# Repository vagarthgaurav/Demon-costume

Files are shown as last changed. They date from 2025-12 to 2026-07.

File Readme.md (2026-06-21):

# Demon Costume

This project is the electronics part of a demon costume. The costume is a work in progress. The hardware design is completed. It will be eventually be integrated into the costume which is intended to be worn in festivals. 

It contains three custom PCBs. The wings open and close driven by linear actuators. It can also drive multiple RGB led chains. It is controlled wirelessly with a remote.

---

## demonBoard



The Main controller. ESP32-C3 Wroom drives two linear actuators for the wings and has connectors for the LED boards. It is powered by a 3S Lipo. 

---

## demonSpawn



The remote that controls the main board. Also an ESP32-C3 Wroom, talks to the demonBoard over ESP-now protocol. It is powered by 18650 Li-Ion cell with USB-C charging. Has 5V LED outputs so it can be integrated into something like a sword.

---

## demonLight



Small board with a single WS2813B RGB LED. Boards can be chained together and they are screwed onto 3D printed thorns.



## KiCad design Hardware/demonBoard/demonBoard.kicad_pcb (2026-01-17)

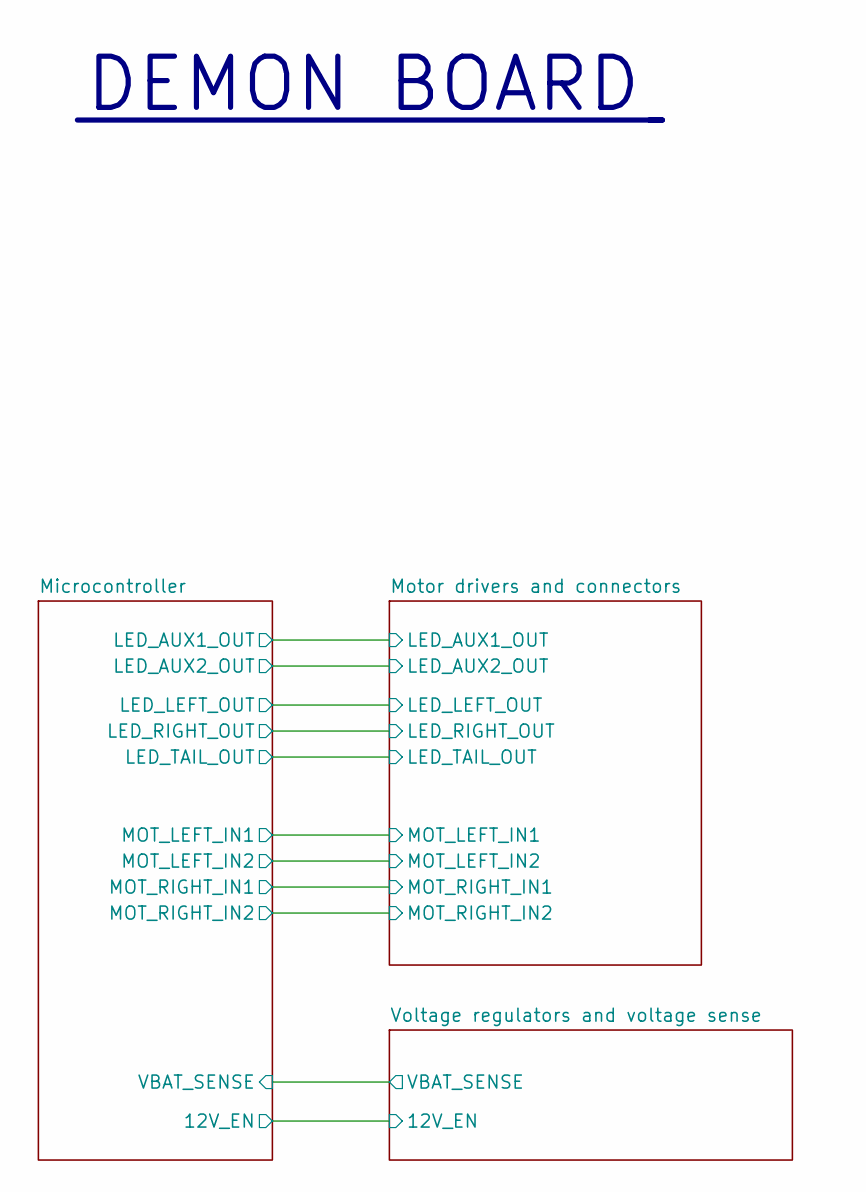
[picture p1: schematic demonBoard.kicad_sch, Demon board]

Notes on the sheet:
DEMON BOARD

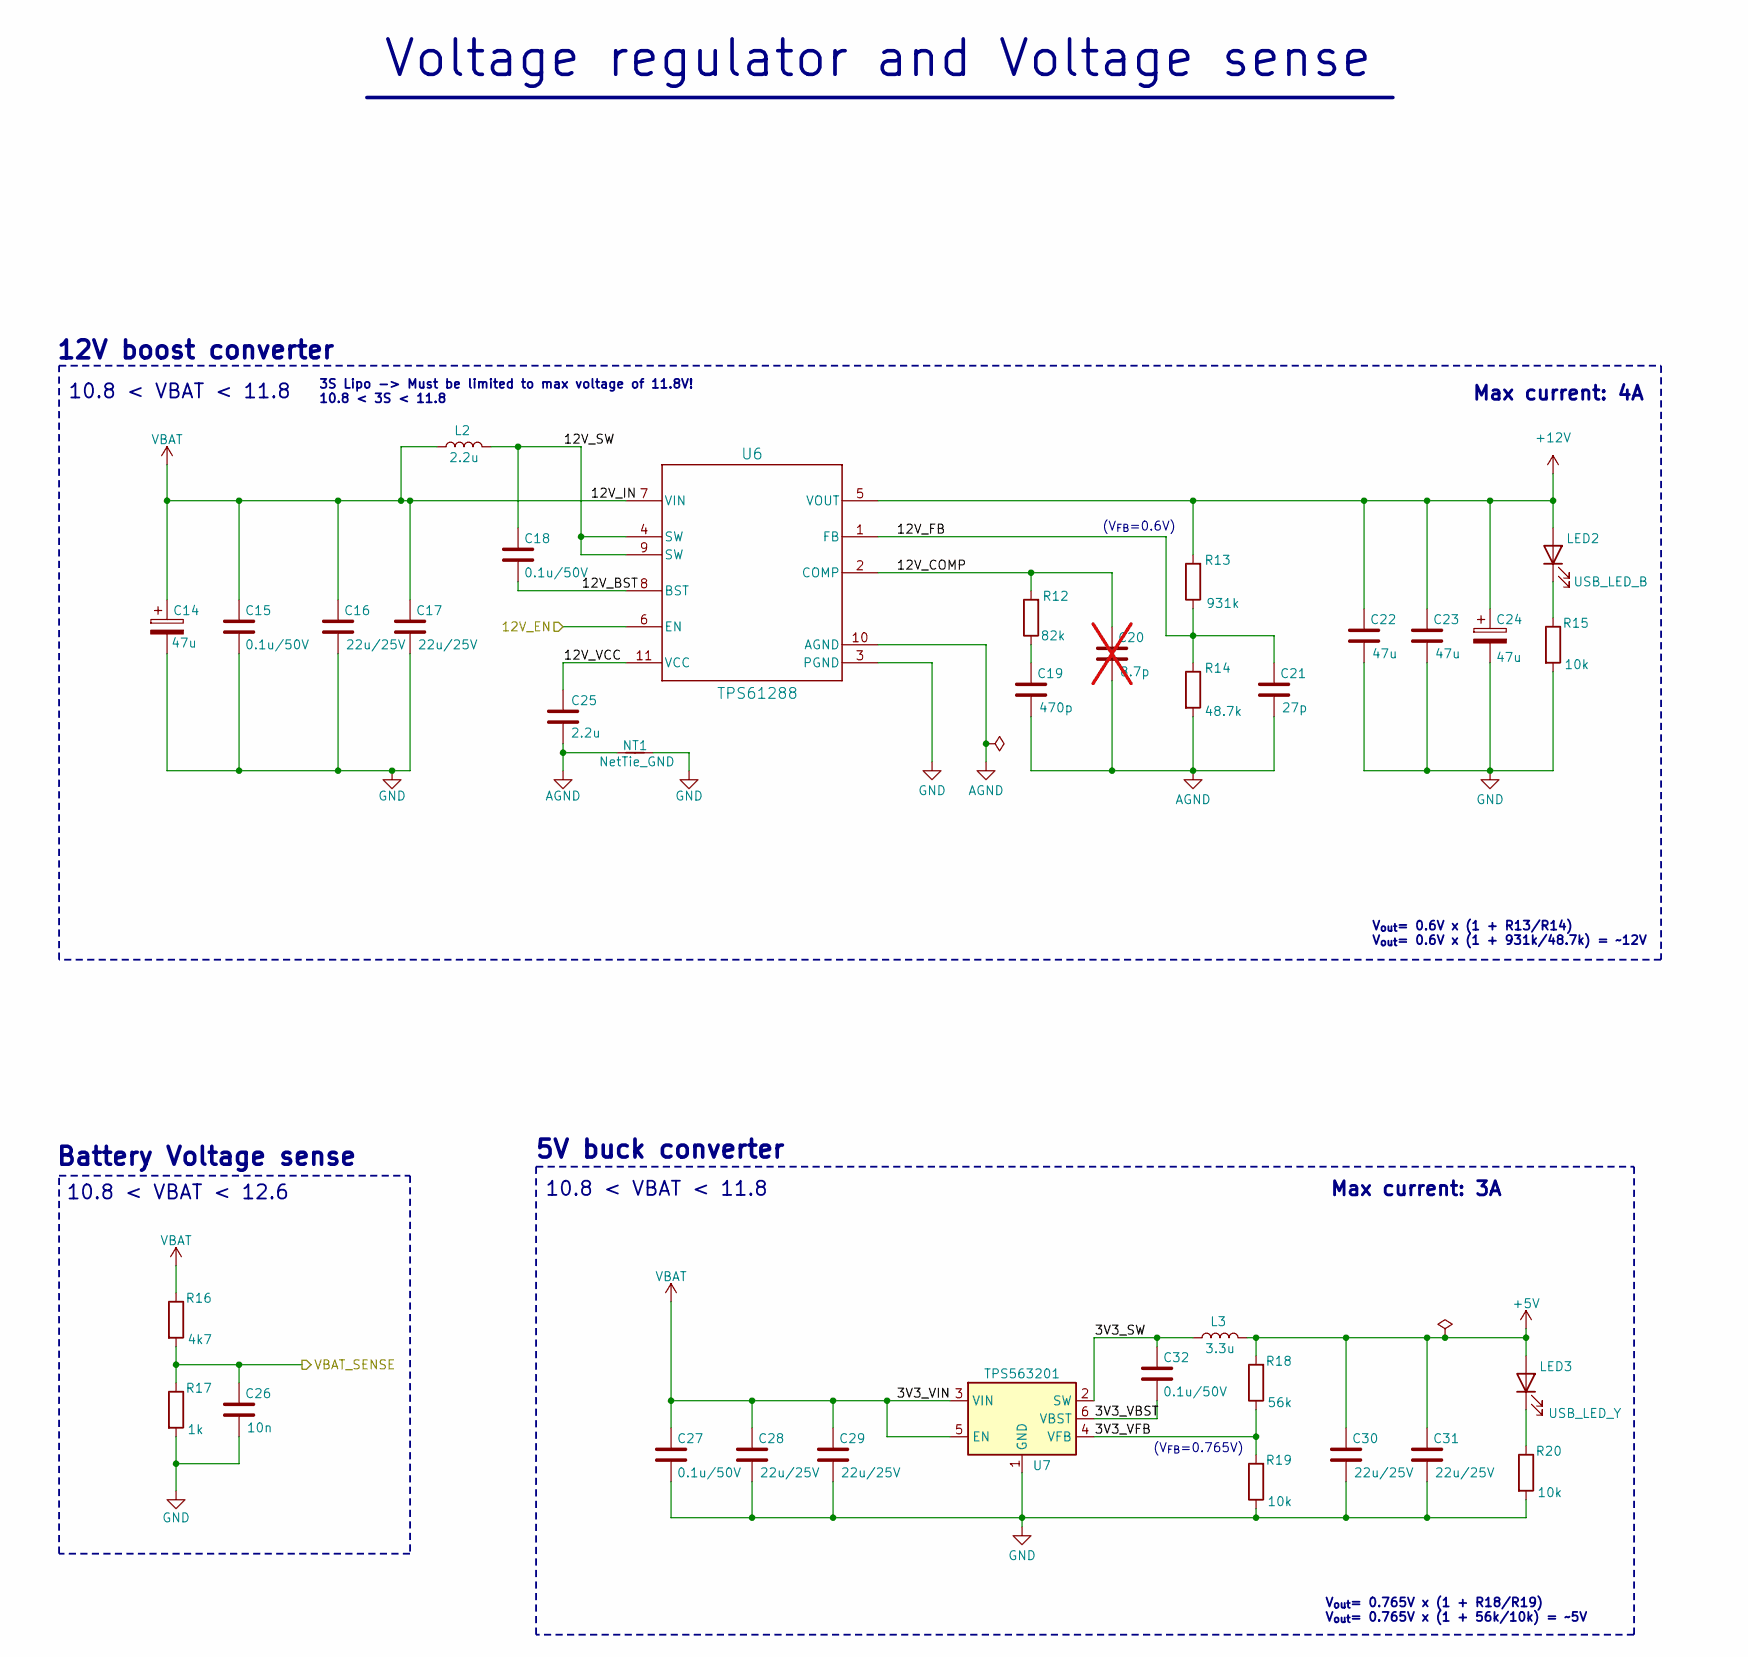
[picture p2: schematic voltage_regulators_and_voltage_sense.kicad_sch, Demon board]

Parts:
C14, C24: 47u; CP_Elec_6.3x7.7
C15, C18, C27, C32: 0.1u/50V; C_0603_1608Metric
C16, C17, C28, C29, C30, C31: 22u/25V; C_0805_2012Metric
C19: 470p; C_0402_1005Metric
C20: 8.7p; C_0402_1005Metric; not fitted
C21: 27p; C_0402_1005Metric
C22, C23: 47u; C_1210_3225Metric
C25: 2.2u; C_0603_1608Metric
C26: 10n; C_0402_1005Metric
L2: 2.2u; SPM6530
L3: 3.3u; L_APV_APH0530
LED2: USB_LED_B; LED_0402_1005Metric
LED3: USB_LED_Y; LED_0402_1005Metric
NT1: NetTie_GND; NetTie-2_SMD_Pad0.5mm
R12: 82k; R_0402_1005Metric
R13: 931k; R_0402_1005Metric
R14: 48.7k; R_0402_1005Metric
R15, R19, R20: 10k; R_0402_1005Metric
R16: 4k7; R_0402_1005Metric
R17: 1k; R_0402_1005Metric
R18: 56k; R_0402_1005Metric
U6: TPS61288
U7: TPS563201; SOT-23-6

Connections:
+5V: C30.1, C31.1, L3.2, LED3.2 (A), R18.2; also elsewhere on the board
+12V: C22.1, C23.1, C24.1, LED2.2 (A), R13.2, U6.5 (VOUT); also elsewhere on the board
/Microcontroller/12V_EN: U6.6 (EN); also elsewhere on the board
/Microcontroller/VBAT_SENSE: C26.1, R16.2, R17.1; also elsewhere on the board
/Voltage regulators and voltage sense/3V3_SW: C32.1, L3.1, U7.2 (SW)
/Voltage regulators and voltage sense/3V3_VBST: C32.2, U7.6 (VBST)
/Voltage regulators and voltage sense/3V3_VFB: R18.1, R19.2, U7.4 (VFB)
/Voltage regulators and voltage sense/12V_BST: C18.2, U6.8 (BST)
/Voltage regulators and voltage sense/12V_COMP: C20.1, R12.2, U6.2 (COMP)
/Voltage regulators and voltage sense/12V_FB: C21.1, R13.1, R14.1, U6.1 (FB)
/Voltage regulators and voltage sense/12V_SW: C18.1, L2.2, U6.4 (SW), U6.9 (SW)
/Voltage regulators and voltage sense/12V_VCC: C25.1, U6.11 (VCC)
AGND: C19.2, C20.2, C21.2, C25.2, NT1.1, R14.2, U6.10 (AGND)
GND: C14.2, C15.2, C16.2, C17.2, C22.2, C23.2, C24.2, C26.2, C27.2, C28.2, C29.2, C30.2, C31.2, NT1.2, R15.2, R17.2, R19.1, R20.2, U6.3 (PGND), U7.1 (GND); also elsewhere on the board
unnamed: C19.1, R12.1
unnamed: LED2.1 (K), R15.1
unnamed: LED3.1 (K), R20.1
VBAT: C14.1, C15.1, C16.1, C17.1, C27.1, C28.1, C29.1, L2.1, R16.1, U6.7 (VIN), U7.3 (VIN), U7.5 (EN); also elsewhere on the board

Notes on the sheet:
Battery Voltage sense
10.8 < VBAT < 11.8
Max current: 3A
Voltage regulator and Voltage sense
Max current: 4A
3S Lipo -> Must be limited to max voltage of 11.8V! 10.8 < 3S < 11.8
5V buck converter
(V_{FB}=0.6V)
(V_{FB}=0.765V)
V_{out}= 0.6V x (1 + R13/R14) V_{out}= 0.6V x (1 + 931k/48.7k) = ~12V
10.8 < VBAT < 12.6
V_{out}= 0.765V x (1 + R18/R19) V_{out}= 0.765V x (1 + 56k/10k) = ~5V
12V boost converter

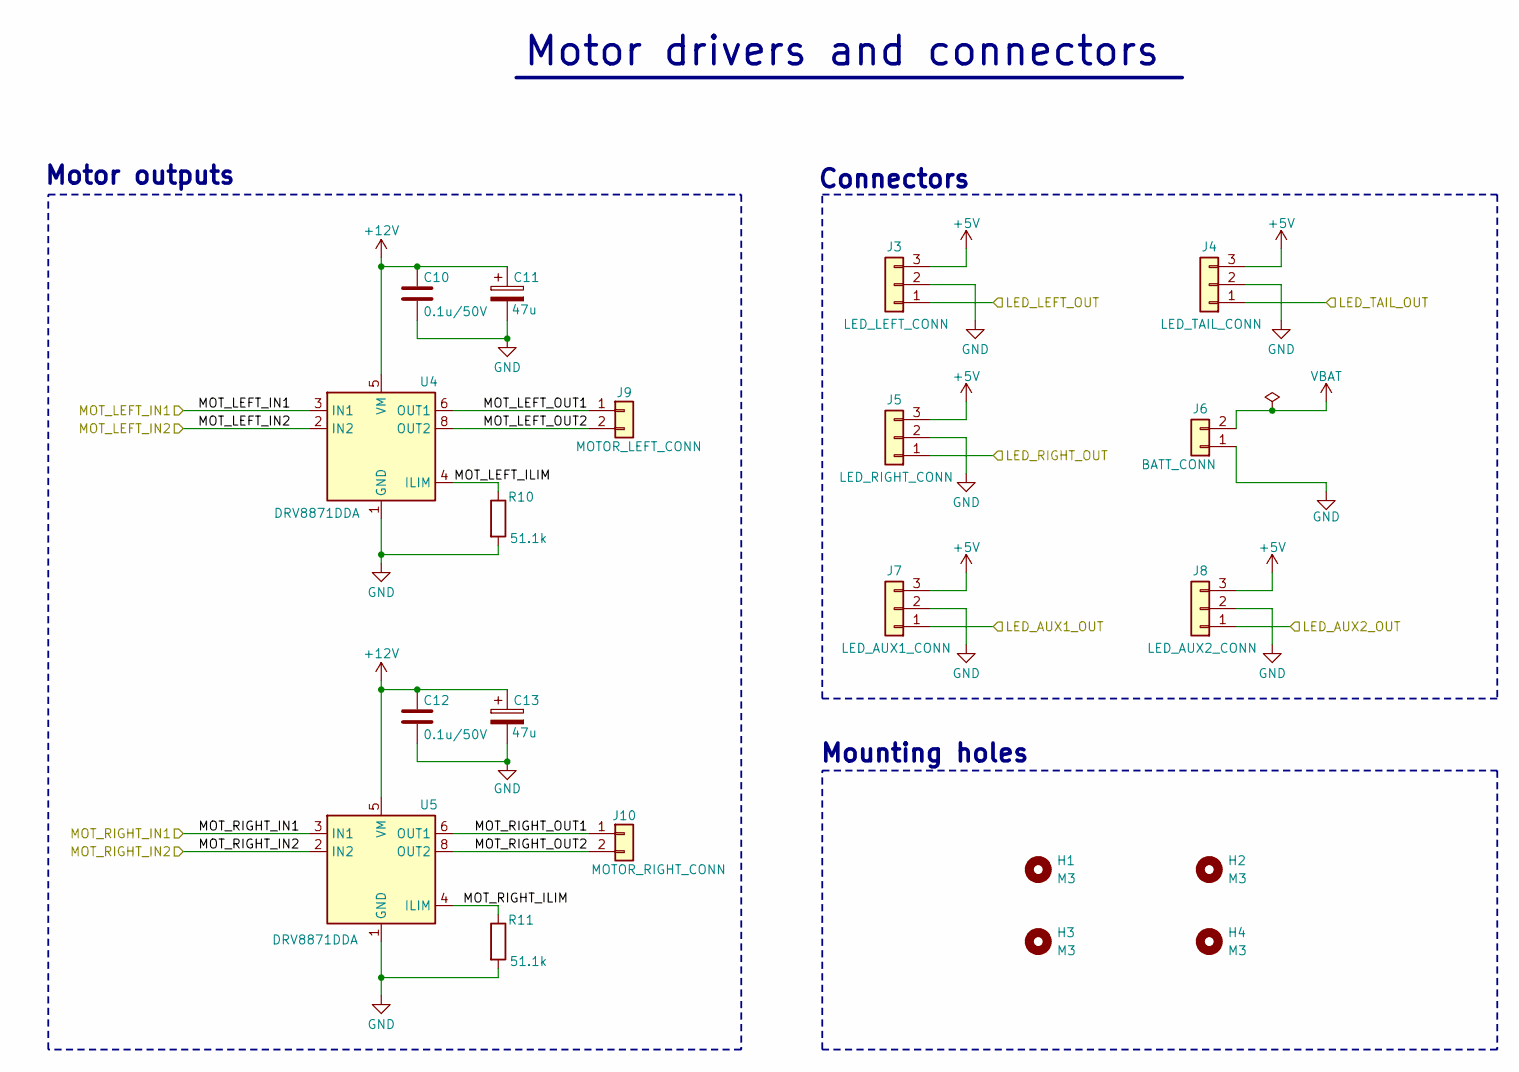
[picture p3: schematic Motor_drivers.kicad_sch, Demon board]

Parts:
C10, C12: 0.1u/50V; C_0603_1608Metric
C11, C13: 47u; CP_Elec_6.3x7.7
H1, H2, H3, H4: M3; MountingHole_3.2mm_M3_ISO14580_Pad_TopBottom
J3: LED_LEFT_CONN; JST_PH_S3B-PH-K_1x03_P2.00mm_Horizontal
J4: LED_TAIL_CONN; JST_PH_S3B-PH-K_1x03_P2.00mm_Horizontal
J5: LED_RIGHT_CONN; JST_PH_S3B-PH-K_1x03_P2.00mm_Horizontal
J6: BATT_CONN; AMASS_XT60PW-M_1x02_P7.20mm_Horizontal
J7: LED_AUX1_CONN; JST_PH_S3B-PH-K_1x03_P2.00mm_Horizontal
J8: LED_AUX2_CONN; JST_PH_S3B-PH-K_1x03_P2.00mm_Horizontal
J9: MOTOR_LEFT_CONN; SPTAF_1_ 2-5_0-EL
J10: MOTOR_RIGHT_CONN; SPTAF_1_ 2-5_0-EL
R10, R11: 51.1k; R_0402_1005Metric
U4, U5: DRV8871DDA; Texas_HTSOP-8-1EP_3.9x4.9mm_P1.27mm_EP2.95x4.9mm_Mask2.4x3.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

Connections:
+5V: J3.3, J4.3, J5.3, J7.3, J8.3; also elsewhere on the board
+12V: C10.1, C11.1, C12.1, C13.1, U4.5 (VM), U5.5 (VM); also elsewhere on the board
/Microcontroller/BOOT_SEL_BTN: J7.1; also elsewhere on the board
/Microcontroller/LED_AUX2_OUT: J8.1; also elsewhere on the board
/Microcontroller/LED_LEFT_OUT: J3.1; also elsewhere on the board
/Microcontroller/LED_RIGHT_OUT: J5.1; also elsewhere on the board
/Microcontroller/LED_TAIL_OUT: J4.1; also elsewhere on the board
/Motor drivers and connectors/MOT_LEFT_ILIM: R10.1, U4.4 (ILIM)
/Motor drivers and connectors/MOT_LEFT_IN1: U4.3 (IN1); also elsewhere on the board
/Motor drivers and connectors/MOT_LEFT_IN2: U4.2 (IN2); also elsewhere on the board
/Motor drivers and connectors/MOT_LEFT_OUT1: J9.1, U4.6 (OUT1)
/Motor drivers and connectors/MOT_LEFT_OUT2: J9.2, U4.8 (OUT2)
/Motor drivers and connectors/MOT_RIGHT_ILIM: R11.1, U5.4 (ILIM)
/Motor drivers and connectors/MOT_RIGHT_IN1: U5.3 (IN1); also elsewhere on the board
/Motor drivers and connectors/MOT_RIGHT_IN2: U5.2 (IN2); also elsewhere on the board
/Motor drivers and connectors/MOT_RIGHT_OUT1: J10.1, U5.6 (OUT1)
/Motor drivers and connectors/MOT_RIGHT_OUT2: J10.2, U5.8 (OUT2)
GND: C10.2, C11.2, C12.2, C13.2, J3.2, J4.2, J5.2, J6.1, J7.2, J8.2, R10.2, R11.2, U4.1 (GND), U4.7 (GND), U4.9 (GND), U5.1 (GND), U5.7 (GND), U5.9 (GND); also elsewhere on the board
VBAT: J6.2; also elsewhere on the board

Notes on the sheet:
Mounting holes
Connectors
Motor outputs
Motor drivers and connectors

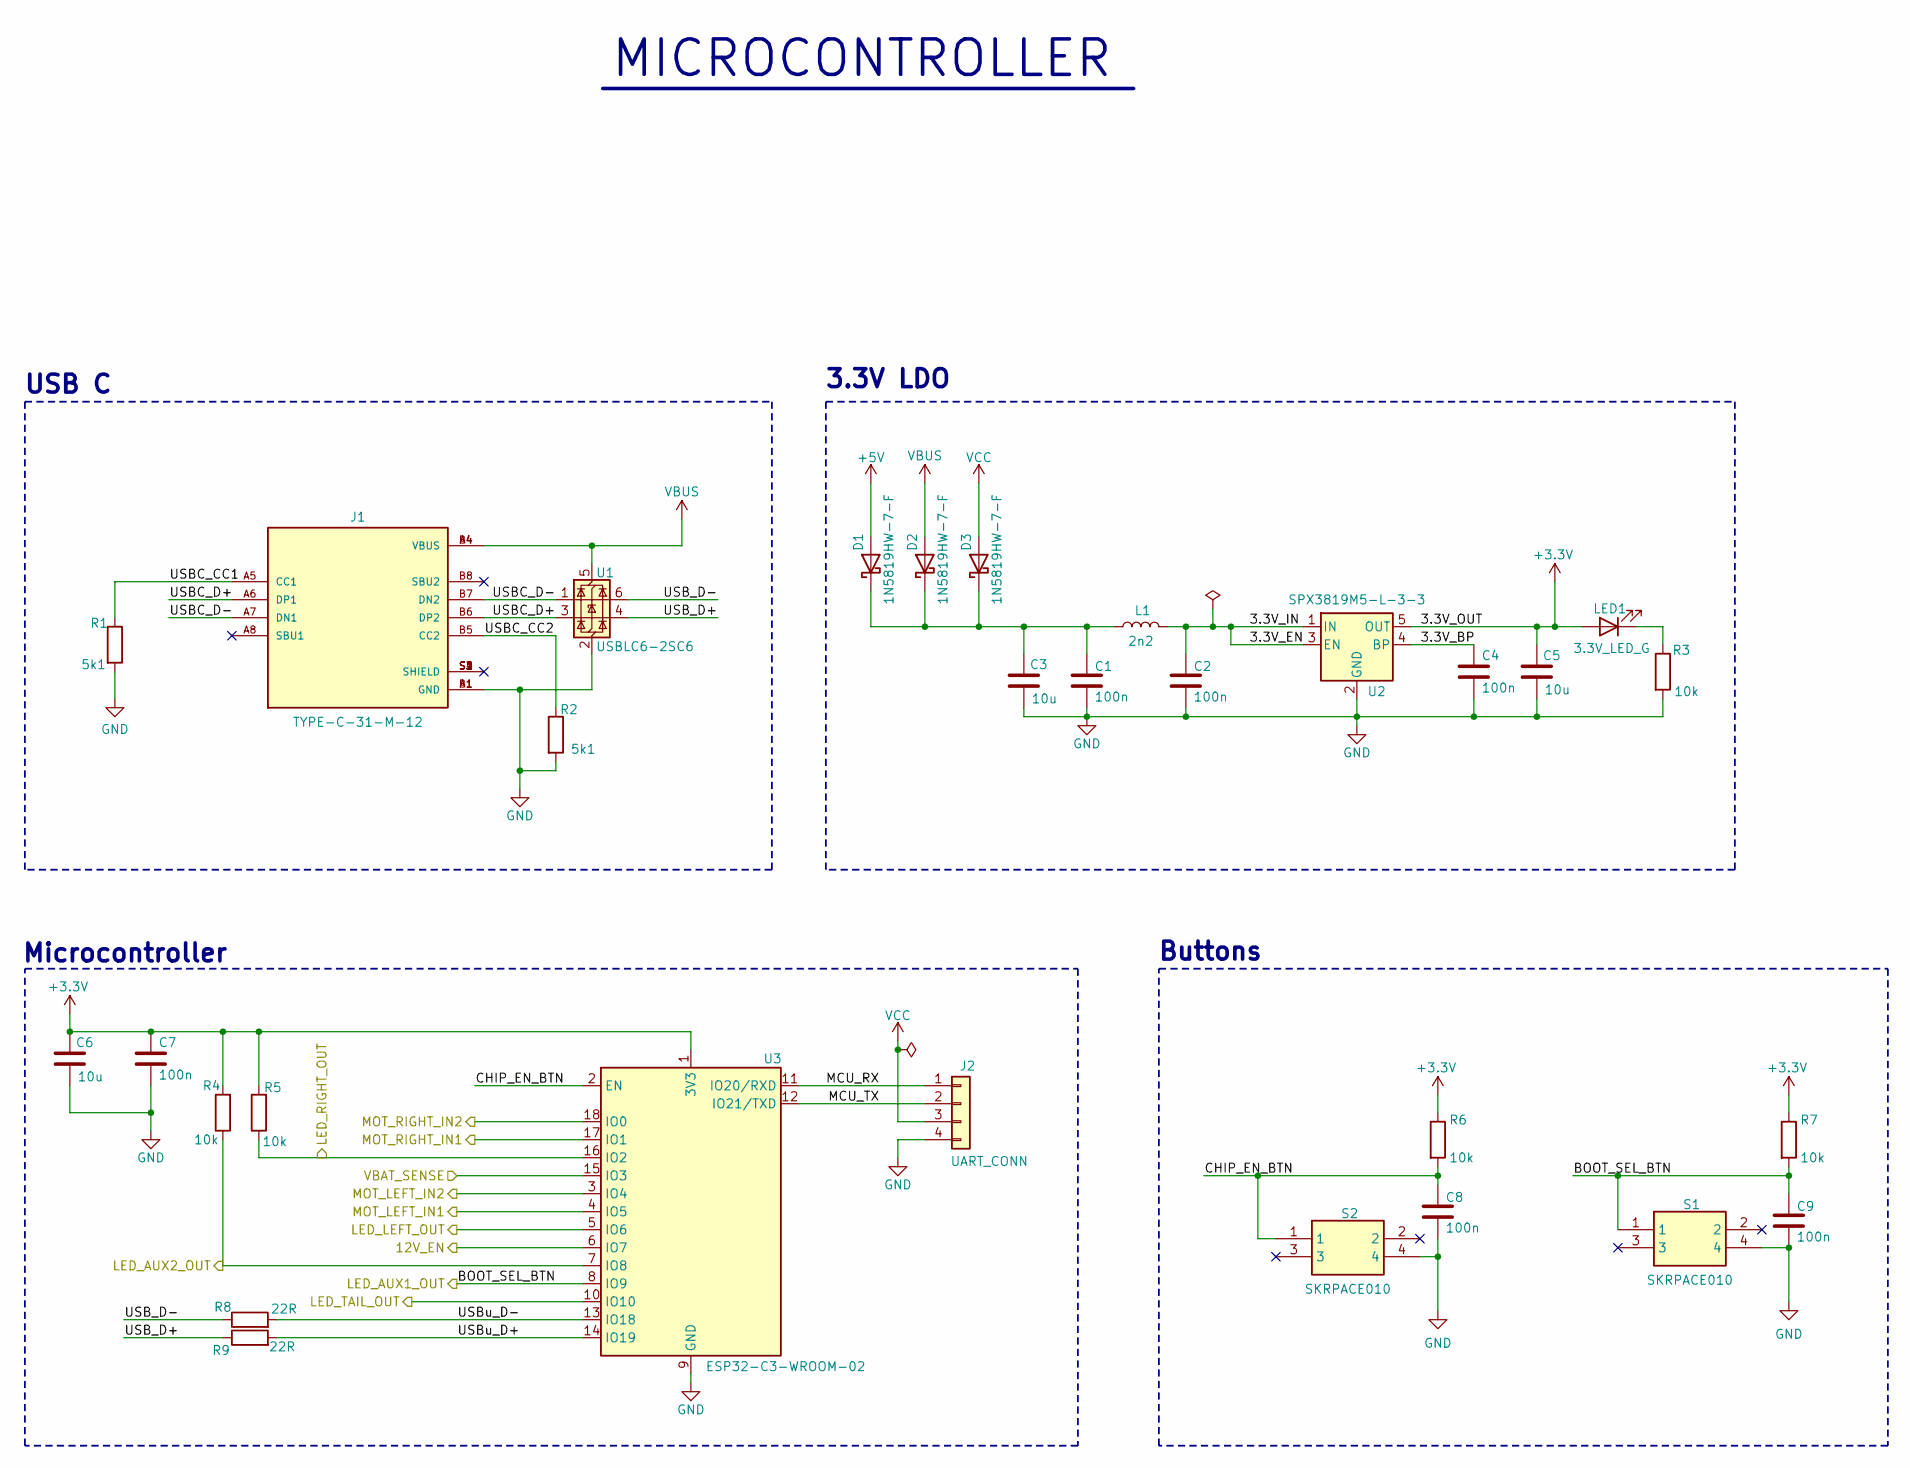
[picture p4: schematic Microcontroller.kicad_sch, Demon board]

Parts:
C1, C2, C4, C7, C8, C9: 100n; C_0402_1005Metric
C3, C5, C6: 10u; C_0603_1608Metric
D1, D2, D3: 1N5819HW-7-F; D_SOD-123
J1: TYPE-C-31-M-12; HRO_TYPE-C-31-M-12; PARTREV 2020.12.08
J2: UART_CONN; PinHeader_1x04_P2.54mm_Vertical
L1: 2n2; L_0402_1005Metric
LED1: 3.3V_LED_G; LED_0402_1005Metric
R1, R2: 5k1; R_0402_1005Metric
R3, R4, R5, R6, R7: 10k; R_0402_1005Metric
R8, R9: 22R; R_0402_1005Metric
S1, S2: SKRPACE010; SKRPARE010; Mouser Part Number 688-SKRPARE010
U1: USBLC6-2SC6; SOT-23-6
U2: SPX3819M5-L-3-3; SOT-23-5
U3: ESP32-C3-WROOM-02

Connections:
+3.3V: C5.1, C6.1, C7.1, LED1.2 (A), R4.2, R5.2, R6.1, R7.1, U2.5 (OUT), U3.1 (3V3)
+5V: D1.2 (A); also elsewhere on the board
/Microcontroller/3.3V_BP: C4.1, U2.4 (BP)
/Microcontroller/3.3V_EN: C2.1, L1.2, U2.1 (IN), U2.3 (EN)
/Microcontroller/12V_EN: U3.6 (IO7); also elsewhere on the board
/Microcontroller/BOOT_SEL_BTN: C9.1, R7.2, S1.1, U3.8 (IO9); also elsewhere on the board
/Microcontroller/CHIP_EN_BTN: C8.1, R6.2, S2.1, U3.2 (EN)
/Microcontroller/LED_AUX2_OUT: R4.1, U3.7 (IO8); also elsewhere on the board
/Microcontroller/LED_LEFT_OUT: U3.5 (IO6); also elsewhere on the board
/Microcontroller/LED_RIGHT_OUT: R5.1, U3.16 (IO2); also elsewhere on the board
/Microcontroller/LED_TAIL_OUT: U3.10 (IO10); also elsewhere on the board
/Microcontroller/MCU_RX: J2.1, U3.11 (IO20/RXD)
/Microcontroller/MCU_TX: J2.2, U3.12 (IO21/TXD)
/Microcontroller/USBC_CC1: J1.A5 (CC1), R1.1
/Microcontroller/USBC_CC2: J1.B5 (CC2), R2.1
/Microcontroller/USBC_D+: J1.A6 (DP1), J1.B6 (DP2), U1.3 (I/O2)
/Microcontroller/USBC_D-: J1.A7 (DN1), J1.B7 (DN2), U1.1 (I/O1)
/Microcontroller/USB_D+: R9.1, U1.4 (I/O2)
/Microcontroller/USB_D-: R8.1, U1.6 (I/O1)
/Microcontroller/USBu_D+: R9.2, U3.14 (IO19)
/Microcontroller/USBu_D-: R8.2, U3.13 (IO18)
/Microcontroller/VBAT_SENSE: U3.15 (IO3); also elsewhere on the board
/Motor drivers and connectors/MOT_LEFT_IN1: U3.4 (IO5); also elsewhere on the board
/Motor drivers and connectors/MOT_LEFT_IN2: U3.3 (IO4); also elsewhere on the board
/Motor drivers and connectors/MOT_RIGHT_IN1: U3.17 (IO1); also elsewhere on the board
/Motor drivers and connectors/MOT_RIGHT_IN2: U3.18 (IO0); also elsewhere on the board
GND: C1.2, C2.2, C3.2, C4.2, C5.2, C6.2, C7.2, C8.2, C9.2, J1.A1 (GND), J1.B1 (GND), J2.4, R1.2, R2.2, R3.2, S1.4, S2.4, U1.2 (GND), U2.2 (GND), U3.9 (GND), U3.19 (GND); also elsewhere on the board
unnamed: C1.1, C3.1, D1.1 (K), D2.1 (K), D3.1 (K), L1.1
unnamed: LED1.1 (K), R3.1
VBUS: D2.2 (A), J1.A4 (VBUS), J1.B4 (VBUS), U1.5 (VBUS)
VCC: D3.2 (A), J2.3

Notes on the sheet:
Microcontroller
MICROCONTROLLER
USB C
3.3V LDO
Buttons

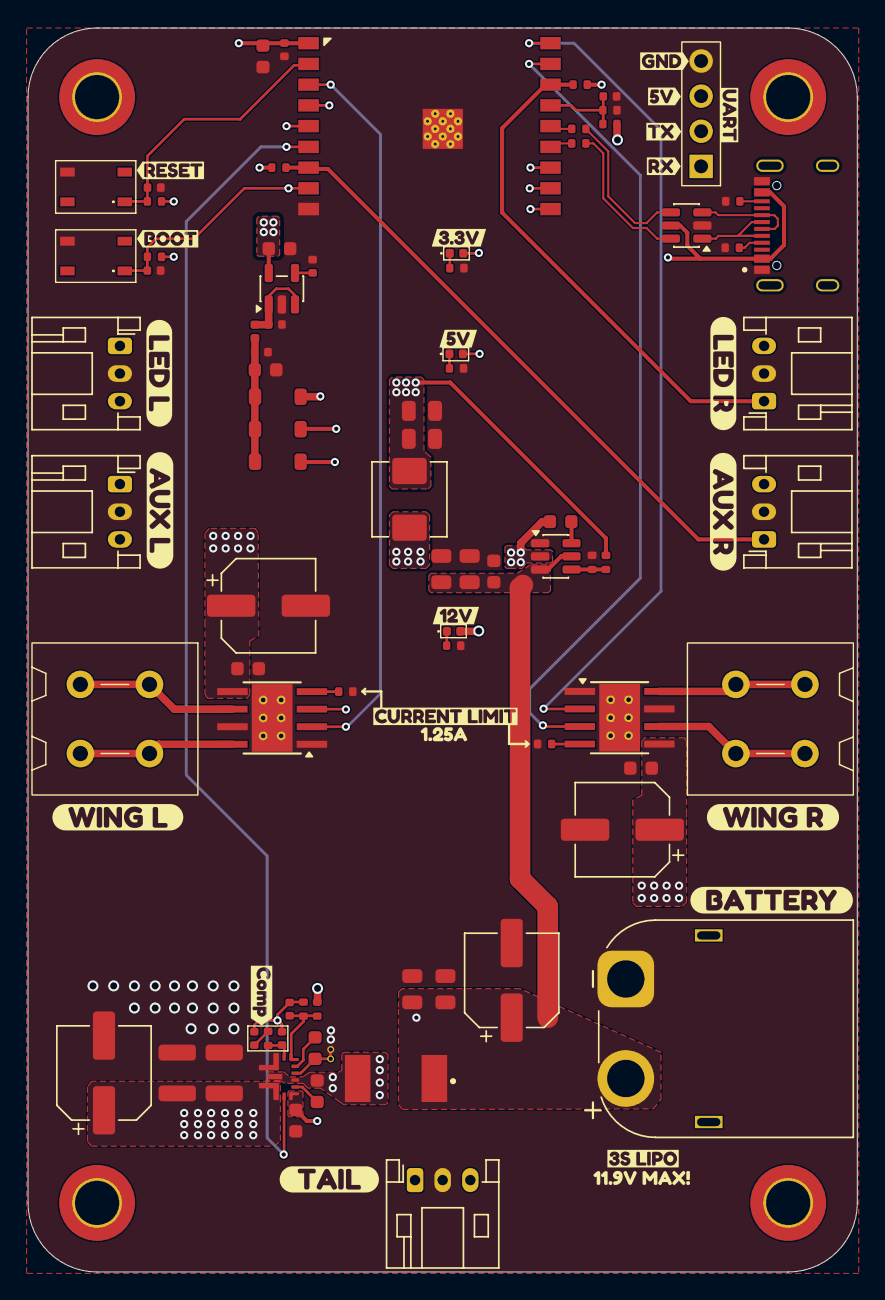
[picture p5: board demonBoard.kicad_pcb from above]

Board: 6 copper layers, 60.0 x 90.0 mm, 108 parts (0 on the bottom side), 51 nets.

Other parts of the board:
kibuzzard-692F179E: G***; kibuzzard-692F179E
kibuzzard-6926C2DC: G***; kibuzzard-6926C2DC
kibuzzard-6926C4A5: G***; kibuzzard-6926C4A5
kibuzzard-6926C4D4: G***; kibuzzard-6926C4D4
kibuzzard-6926C5ED: G***; kibuzzard-6926C5ED
kibuzzard-6926C39D: G***; kibuzzard-6926C39D
kibuzzard-6926C40E: G***; kibuzzard-6926C40E
kibuzzard-6926C80F: G***; kibuzzard-6926C80F
kibuzzard-6926C366: G***; kibuzzard-6926C366
kibuzzard-6926C403: G***; kibuzzard-6926C403
kibuzzard-6926C417: G***; kibuzzard-6926C417
kibuzzard-6926C440: G***; kibuzzard-6926C440
kibuzzard-6926C482: G***; kibuzzard-6926C482
kibuzzard-6926C559: G***; kibuzzard-6926C559
kibuzzard-6926C567: G***; kibuzzard-6926C567
kibuzzard-6926C685: G***; kibuzzard-6926C685
kibuzzard-6926C771: G***; kibuzzard-6926C771
kibuzzard-6926C831: G***; kibuzzard-6926C831
kibuzzard-6926C843: G***; kibuzzard-6926C843
kibuzzard-6926C976: G***; kibuzzard-6926C976
kibuzzard-6926C980: G***; kibuzzard-6926C980
kibuzzard-6926CDBB: G***; kibuzzard-6926CDBB
kibuzzard-69304D0B: G***; kibuzzard-69304D0B

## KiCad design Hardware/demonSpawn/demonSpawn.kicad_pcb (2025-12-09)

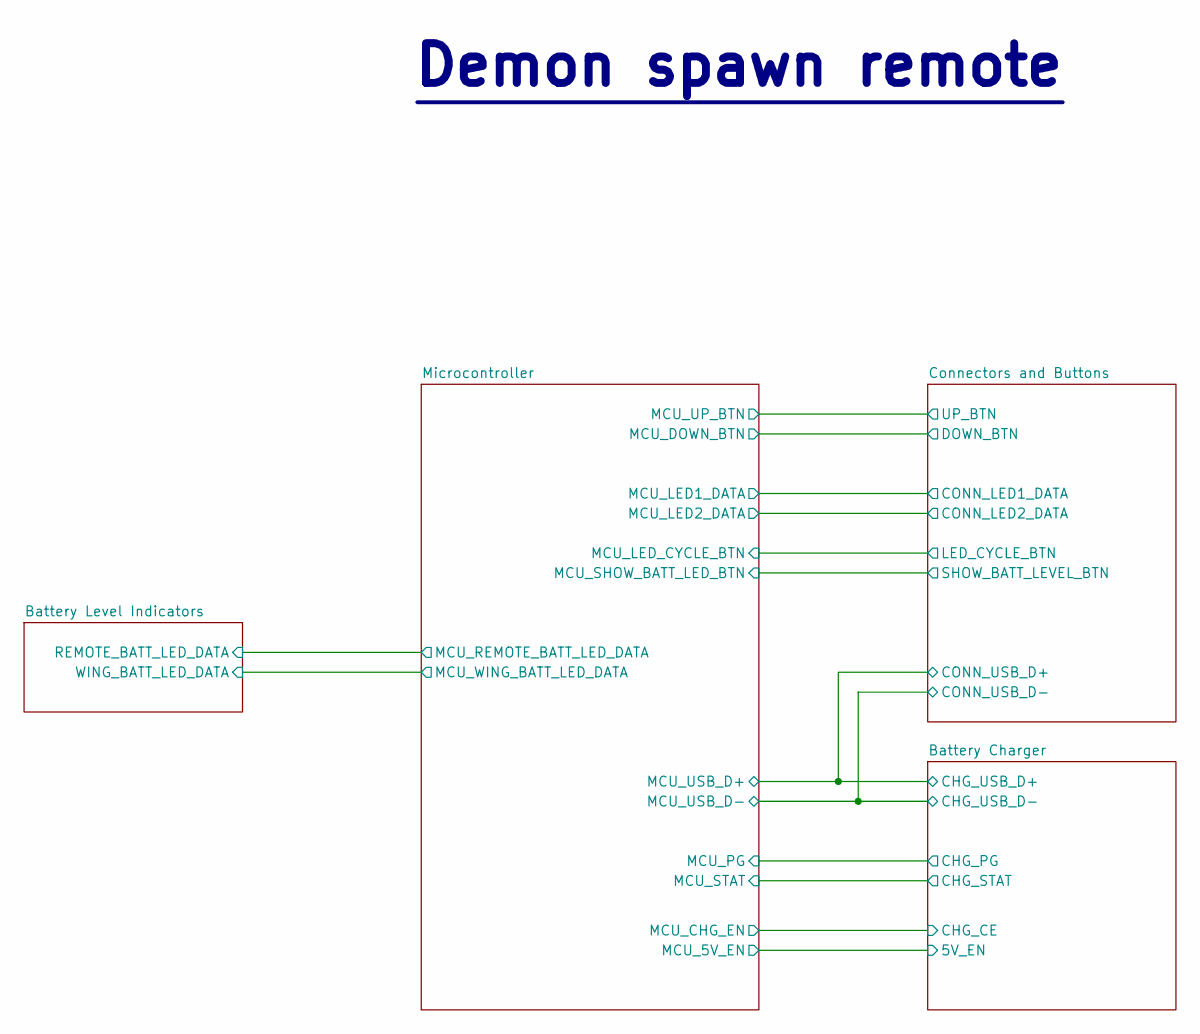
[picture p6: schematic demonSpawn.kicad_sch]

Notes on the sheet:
Demon spawn remote

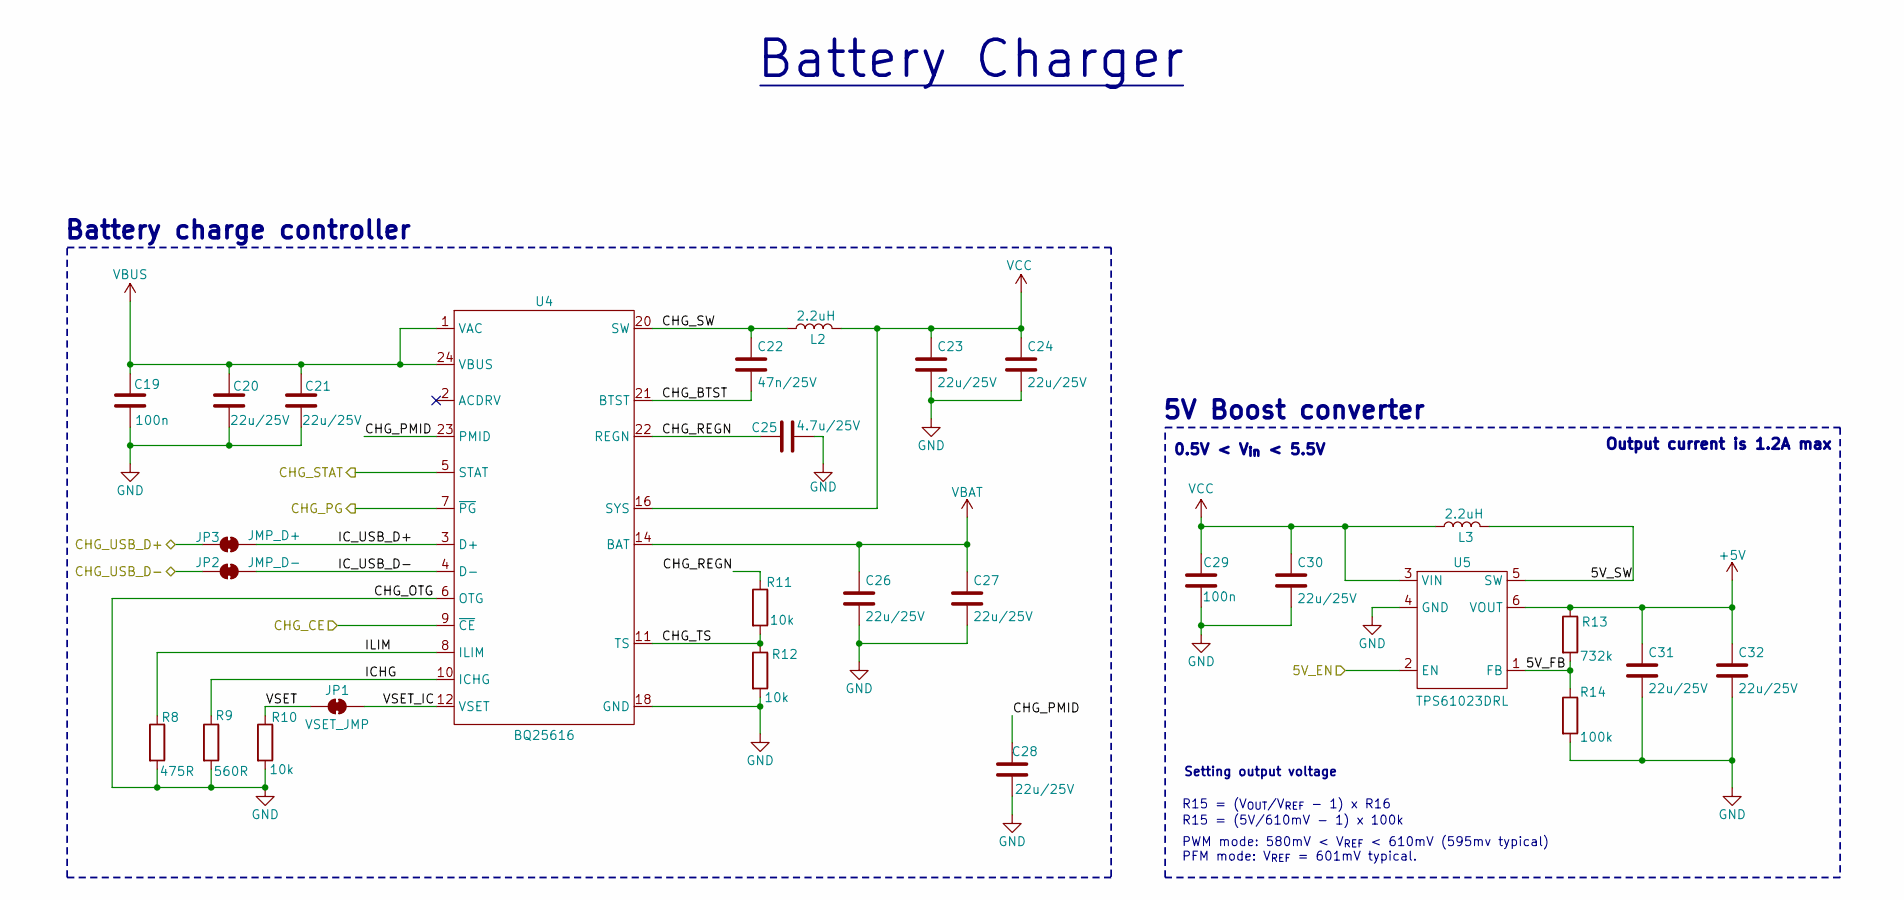
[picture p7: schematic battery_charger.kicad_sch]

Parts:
C19, C29: 100n; C_0402_1005Metric
C20, C21, C23, C24, C26, C27, C28, C30, C31, C32: 22u/25V; C_0805_2012Metric
C22: 47n/25V; C_0402_1005Metric
C25: 4.7u/25V; C_0603_1608Metric
JP1: VSET_JMP; SolderJumper-2_P1.3mm_Bridged_RoundedPad1.0x1.5mm
JP2: JMP_D-; SolderJumper-2_P1.3mm_Bridged_RoundedPad1.0x1.5mm
JP3: JMP_D+; SolderJumper-2_P1.3mm_Bridged_RoundedPad1.0x1.5mm
L2, L3: 2.2uH; L_Taiyo-Yuden_NR-40xx
R8: 475R; R_0402_1005Metric
R9: 560R; R_0402_1005Metric
R10, R11, R12: 10k; R_0402_1005Metric
R13: 732k; R_0402_1005Metric
R14: 100k; R_0402_1005Metric
U4: BQ25616; WQFN24_RTW_TEX-L
U5: TPS61023DRL; SOTFL50P160X60-6N

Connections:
+5V: C31.1, C32.1, R13.1, U5.6 (VOUT); also elsewhere on the board
/Battery Charger/5V_EN: U5.2 (EN); also elsewhere on the board
/Battery Charger/5V_FB: R13.2, R14.1, U5.1 (FB)
/Battery Charger/5V_SW: L3.2, U5.5 (SW)
/Battery Charger/CHG_BTST: C22.2, U4.21 (BTST)
/Battery Charger/CHG_CE: U4.9 (~CE); also elsewhere on the board
/Battery Charger/CHG_PG: U4.7 (~PG); also elsewhere on the board
/Battery Charger/CHG_PMID: C28.2, U4.23 (PMID)
/Battery Charger/CHG_REGN: C25.1, R11.1, U4.22 (REGN)
/Battery Charger/CHG_STAT: U4.5 (STAT); also elsewhere on the board
/Battery Charger/CHG_SW: C22.1, L2.1, U4.19 (SW), U4.20 (SW)
/Battery Charger/CHG_TS: R11.2, R12.1, U4.11 (TS)
/Battery Charger/CHG_USB_D+: JP3.1 (A); also elsewhere on the board
/Battery Charger/CHG_USB_D-: JP2.1 (A); also elsewhere on the board
/Battery Charger/ICHG: R9.1, U4.10 (ICHG)
/Battery Charger/IC_USB_D+: JP3.2 (B), U4.3 (D+)
/Battery Charger/IC_USB_D-: JP2.2 (B), U4.4 (D-)
/Battery Charger/ILIM: R8.1, U4.8 (ILIM)
/Battery Charger/VSET: JP1.1 (A), R10.1
/Battery Charger/VSET_IC: JP1.2 (B), U4.12 (VSET)
GND: C19.1, C20.1, C21.1, C23.2, C24.2, C25.2, C26.2, C27.2, C28.1, C29.1, C30.2, C31.2, C32.2, R8.2, R9.2, R10.2, R12.2, R14.2, U4.6 (OTG), U4.17 (GND), U4.18 (GND), U4.25 (GND), U5.4 (GND); also elsewhere on the board
VBAT: C26.1, C27.1, U4.13 (BAT), U4.14 (BAT); also elsewhere on the board
VBUS: C19.2, C20.2, C21.2, U4.1 (VAC), U4.24 (VBUS); also elsewhere on the board
VCC: C23.1, C24.1, C29.2, C30.1, L2.2, L3.1, U4.15 (SYS), U4.16 (SYS), U5.3 (VIN); also elsewhere on the board

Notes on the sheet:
0.5V < V_{in} < 5.5V
Setting output voltage
Battery Charger
R15 = (5V/610mV - 1) x 100k
R15 = (V_{OUT}/V_{REF} - 1) x R16
PWM mode: 580mV < V_{REF} < 610mV (595mv typical) PFM mode: V_{REF} = 601mV typical.
Output current is 1.2A max
Battery charge controller
5V Boost converter

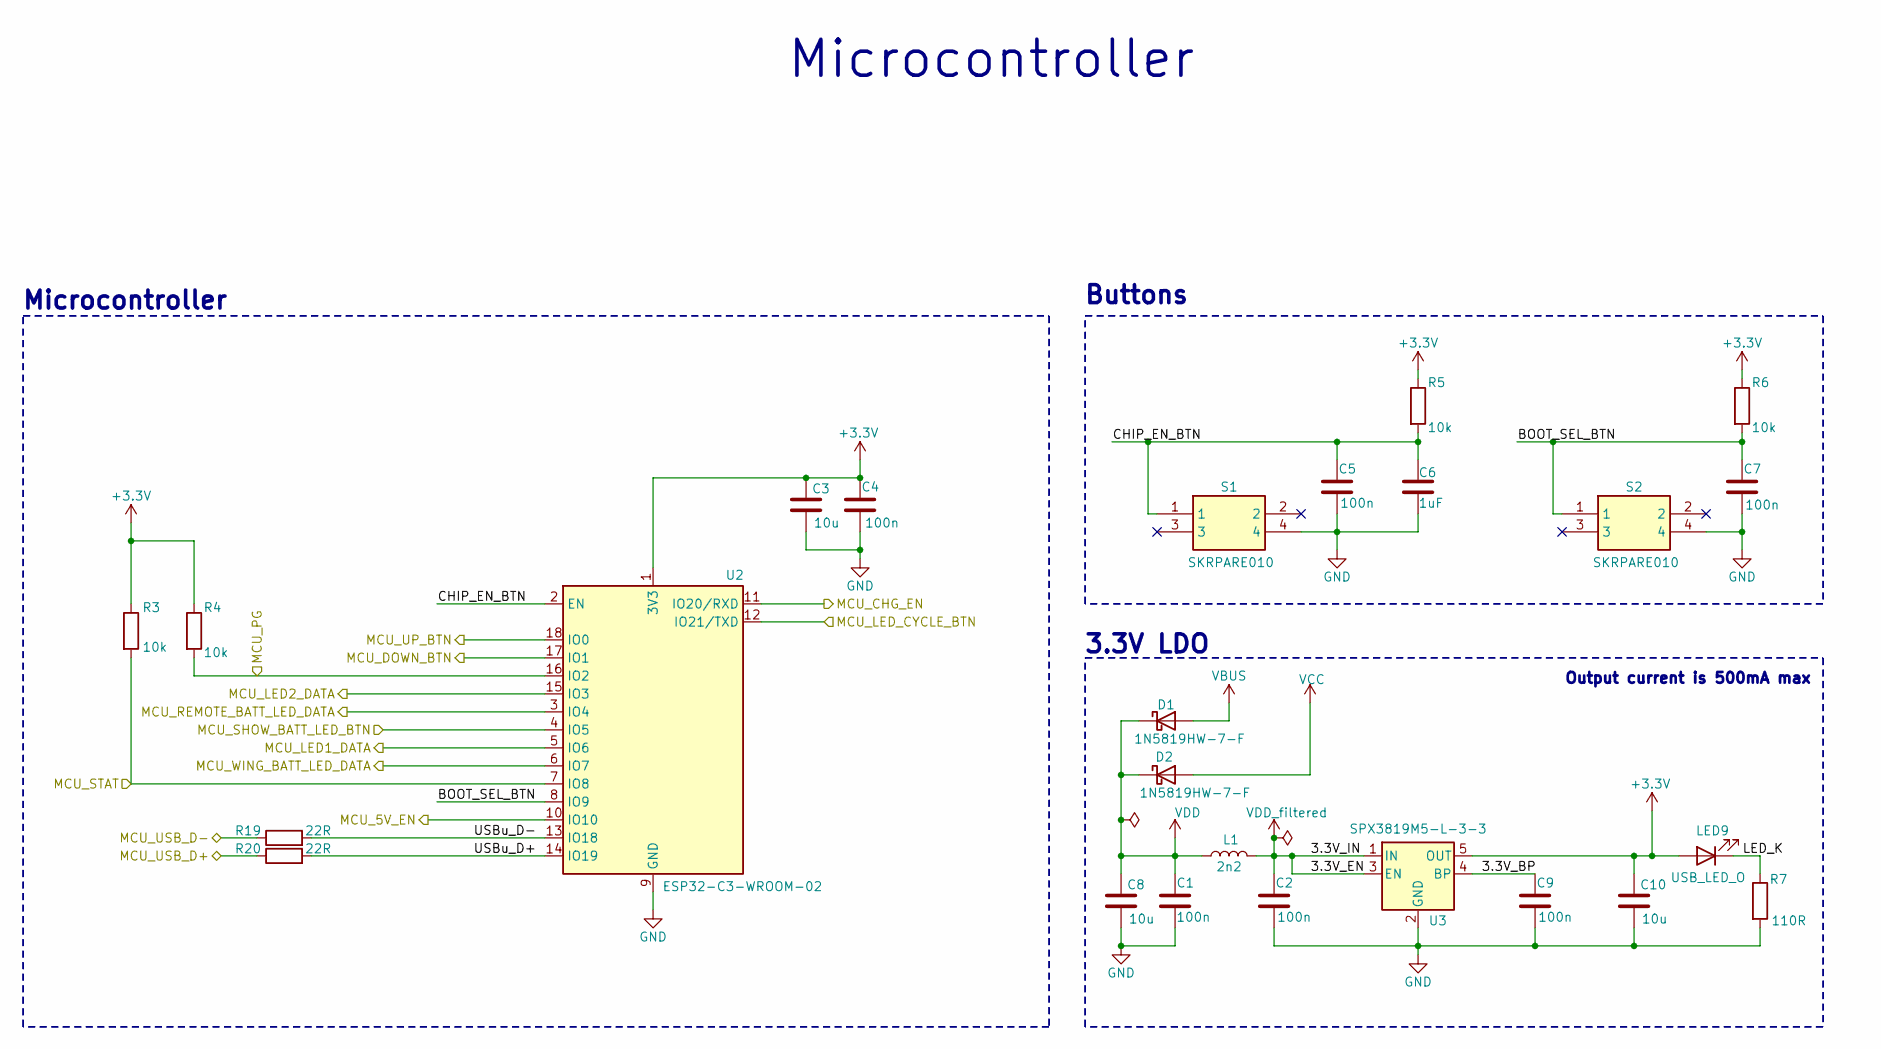
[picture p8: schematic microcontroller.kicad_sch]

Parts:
C1, C2, C4, C5, C7, C9: 100n; C_0402_1005Metric
C3, C8, C10: 10u; C_0603_1608Metric
C6: 1uF; C_0402_1005Metric
D1, D2: 1N5819HW-7-F; D_SOD-123
L1: 2n2; L_0402_1005Metric
LED9: USB_LED_O; LED_0402_1005Metric
R3, R4, R5, R6: 10k; R_0402_1005Metric
R7: 110R; R_0402_1005Metric
R19, R20: 22R; R_0402_1005Metric
S1, S2: SKRPARE010; Mouser Part Number 688-SKRPARE010
U2: ESP32-C3-WROOM-02
U3: SPX3819M5-L-3-3; SOT-23-5

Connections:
+3.3V: C3.1, C4.2, C10.1, LED9.2 (A), R3.1, R4.1, R5.1, R6.1, U2.1 (3V3), U3.5 (OUT); also elsewhere on the board
/Battery Charger/5V_EN: U2.10 (IO10); also elsewhere on the board
/Battery Charger/CHG_CE: U2.11 (IO20/RXD); also elsewhere on the board
/Battery Charger/CHG_PG: R4.2, U2.16 (IO2); also elsewhere on the board
/Battery Charger/CHG_STAT: R3.2, U2.7 (IO8); also elsewhere on the board
/Battery Charger/CHG_USB_D+: R20.1; also elsewhere on the board
/Battery Charger/CHG_USB_D-: R19.1; also elsewhere on the board
/Battery Level Indicators/REMOTE_BATT_LED_DATA: U2.3 (IO4); also elsewhere on the board
/Battery Level Indicators/WING_BATT_LED_DATA: U2.6 (IO7); also elsewhere on the board
/Connectors and Buttons/CONN_LED1_DATA: U2.5 (IO6); also elsewhere on the board
/Connectors and Buttons/CONN_LED2_DATA: U2.15 (IO3); also elsewhere on the board
/Connectors and Buttons/DOWN_BTN: U2.17 (IO1); also elsewhere on the board
/Connectors and Buttons/LED_CYCLE_BTN: U2.12 (IO21/TXD); also elsewhere on the board
/Connectors and Buttons/SHOW_BATT_LEVEL_BTN: U2.4 (IO5); also elsewhere on the board
/Connectors and Buttons/UP_BTN: U2.18 (IO0); also elsewhere on the board
/Microcontroller/3.3V_BP: C9.2, U3.4 (BP)
/Microcontroller/BOOT_SEL_BTN: C7.2, R6.2, S2.1, U2.8 (IO9)
/Microcontroller/CHIP_EN_BTN: C5.2, C6.1, R5.2, S1.1, U2.2 (EN)
/Microcontroller/LED_K: LED9.1 (K), R7.1
/Microcontroller/USBu_D+: R20.2, U2.14 (IO19)
/Microcontroller/USBu_D-: R19.2, U2.13 (IO18)
GND: C1.1, C2.1, C3.2, C4.1, C5.1, C6.2, C7.1, C8.2, C9.1, C10.2, R7.2, S1.4, S2.4, U2.9 (GND), U2.19 (GND), U3.2 (GND); also elsewhere on the board
VBUS: D1.2 (A); also elsewhere on the board
VCC: D2.2 (A); also elsewhere on the board
VDD: C1.2, C8.1, D1.1 (K), D2.1 (K), L1.1
VDD_filtered: C2.2, L1.2, U3.1 (IN), U3.3 (EN)

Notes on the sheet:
Output current is 500mA max
Microcontroller
Microcontroller
Buttons
3.3V LDO

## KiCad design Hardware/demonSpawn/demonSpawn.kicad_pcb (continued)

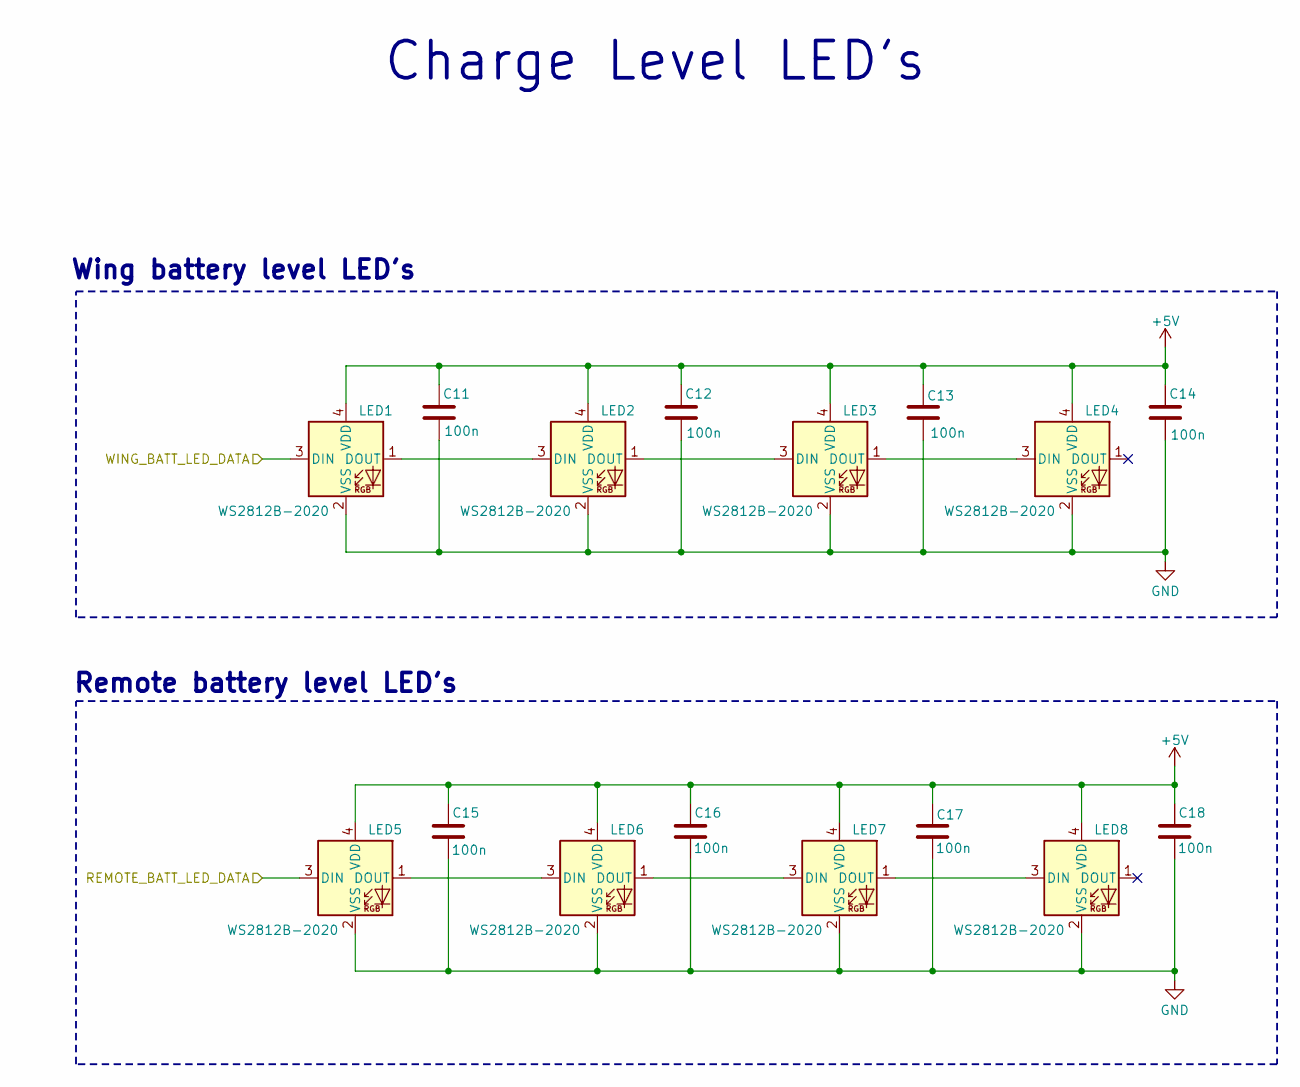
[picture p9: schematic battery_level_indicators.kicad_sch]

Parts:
C11, C12, C13, C14, C15, C16, C17, C18: 100n; C_0402_1005Metric
LED1, LED2, LED3, LED4, LED5, LED6, LED7, LED8: WS2812B-2020; LED_WS2812B-2020_PLCC4_2.0x2.0mm

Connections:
+5V: C11.2, C12.2, C13.2, C14.2, C15.2, C16.2, C17.2, C18.2, LED1.4 (VDD), LED2.4 (VDD), LED3.4 (VDD), LED4.4 (VDD), LED5.4 (VDD), LED6.4 (VDD), LED7.4 (VDD), LED8.4 (VDD); also elsewhere on the board
/Battery Level Indicators/REMOTE_BATT_LED_DATA: LED5.3 (DIN); also elsewhere on the board
/Battery Level Indicators/WING_BATT_LED_DATA: LED1.3 (DIN); also elsewhere on the board
GND: C11.1, C12.1, C13.1, C14.1, C15.1, C16.1, C17.1, C18.1, LED1.2 (VSS), LED2.2 (VSS), LED3.2 (VSS), LED4.2 (VSS), LED5.2 (VSS), LED6.2 (VSS), LED7.2 (VSS), LED8.2 (VSS); also elsewhere on the board
unnamed: LED1.1 (DOUT), LED2.3 (DIN)
unnamed: LED2.1 (DOUT), LED3.3 (DIN)
unnamed: LED3.1 (DOUT), LED4.3 (DIN)
unnamed: LED5.1 (DOUT), LED6.3 (DIN)
unnamed: LED6.1 (DOUT), LED7.3 (DIN)
unnamed: LED7.1 (DOUT), LED8.3 (DIN)

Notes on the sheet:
Charge Level LED's
Wing battery level LED's
Remote battery level LED's

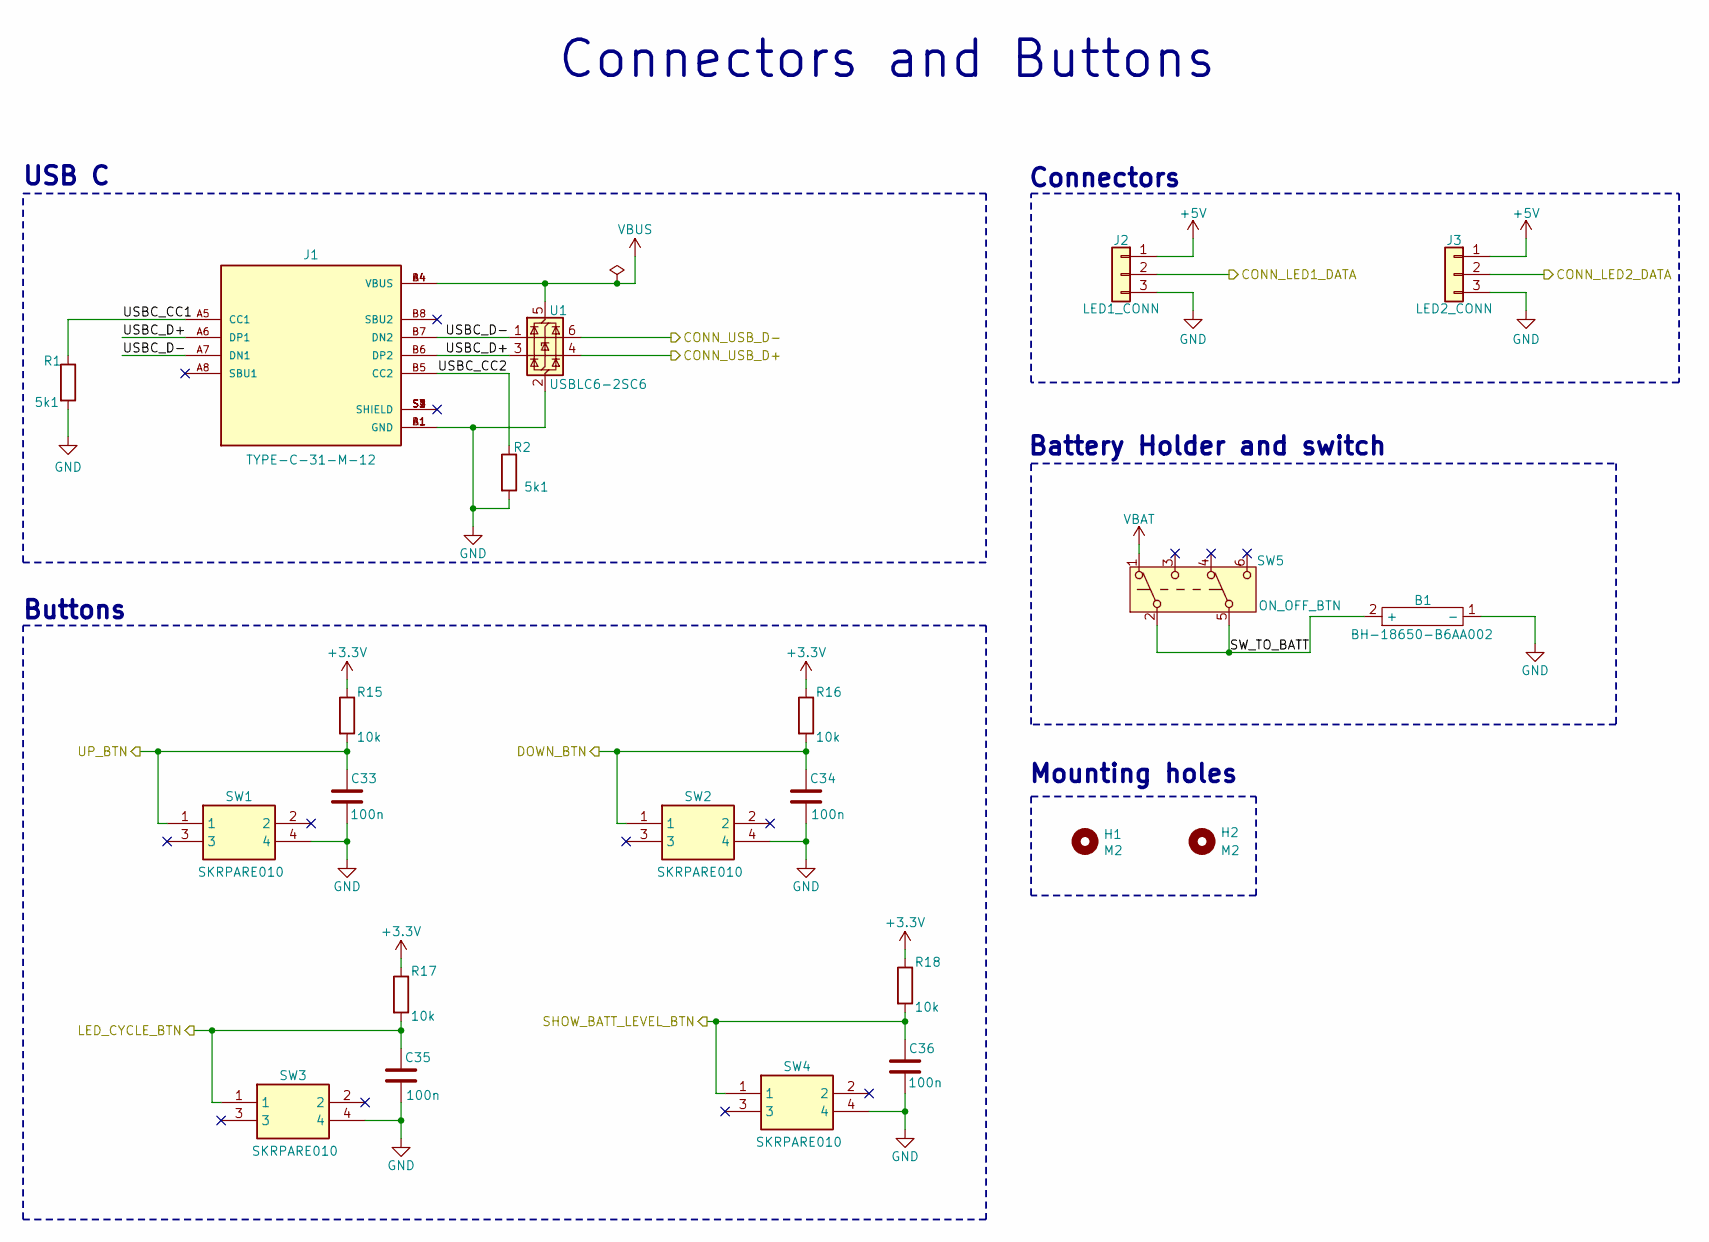
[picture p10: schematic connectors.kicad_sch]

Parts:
B1: BH-18650-B6AA002; BH-18650-B1BA002
C33, C34, C35, C36: 100n; C_0402_1005Metric
H1, H2: M2; MountingHole_2.2mm_M2_DIN965_Pad
J1: TYPE-C-31-M-12; HRO_TYPE-C-31-M-12; PARTREV 2020.12.08
J2: LED1_CONN; JST_PH_S3B-PH-K_1x03_P2.00mm_Horizontal
J3: LED2_CONN; JST_PH_S3B-PH-K_1x03_P2.00mm_Horizontal
R1, R2: 5k1; R_0402_1005Metric
R15, R16, R17, R18: 10k; R_0402_1005Metric
SW1, SW2, SW3, SW4: SKRPARE010; Mouser Part Number 688-SKRPARE010
SW5: ON_OFF_BTN; YIYUAN_YTSPS-22E59NL2
U1: USBLC6-2SC6; SOT-23-6

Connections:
+3.3V: R15.1, R16.1, R17.1, R18.1; also elsewhere on the board
+5V: J2.1, J3.1; also elsewhere on the board
/Battery Charger/CHG_USB_D+: U1.4 (I/O2); also elsewhere on the board
/Battery Charger/CHG_USB_D-: U1.6 (I/O1); also elsewhere on the board
/Connectors and Buttons/CONN_LED1_DATA: J2.2; also elsewhere on the board
/Connectors and Buttons/CONN_LED2_DATA: J3.2; also elsewhere on the board
/Connectors and Buttons/DOWN_BTN: C34.2, R16.2, SW2.1; also elsewhere on the board
/Connectors and Buttons/LED_CYCLE_BTN: C35.2, R17.2, SW3.1; also elsewhere on the board
/Connectors and Buttons/SHOW_BATT_LEVEL_BTN: C36.2, R18.2, SW4.1; also elsewhere on the board
/Connectors and Buttons/SW_TO_BATT: B1.2 (+), SW5.2 (B), SW5.5 (B)
/Connectors and Buttons/UP_BTN: C33.2, R15.2, SW1.1; also elsewhere on the board
/Connectors and Buttons/USBC_CC1: J1.A5 (CC1), R1.1
/Connectors and Buttons/USBC_CC2: J1.B5 (CC2), R2.1
/Connectors and Buttons/USBC_D+: J1.A6 (DP1), J1.B6 (DP2), U1.3 (I/O2)
/Connectors and Buttons/USBC_D-: J1.A7 (DN1), J1.B7 (DN2), U1.1 (I/O1)
GND: B1.1 (-), C33.1, C34.1, C35.1, C36.1, J1.A1 (GND), J1.B1 (GND), J2.3, J3.3, R1.2, R2.2, SW1.4, SW2.4, SW3.4, SW4.4, U1.2 (GND); also elsewhere on the board
VBAT: SW5.1 (A); also elsewhere on the board
VBUS: J1.A4 (VBUS), J1.B4 (VBUS), U1.5 (VBUS); also elsewhere on the board

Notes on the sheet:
USB C
Mounting holes
Battery Holder and switch
Buttons
Connectors and Buttons
Connectors

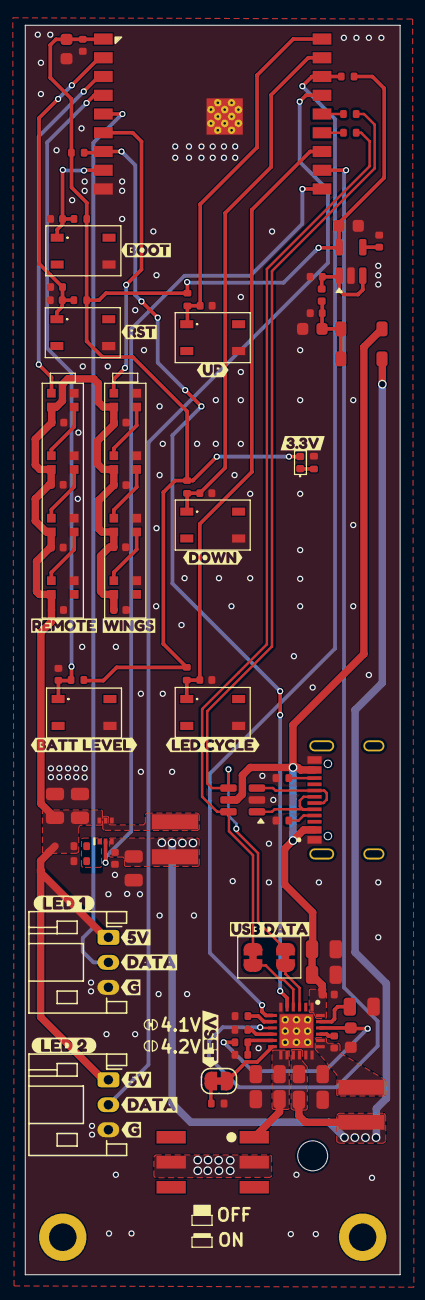
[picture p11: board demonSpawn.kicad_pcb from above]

Board: 4 copper layers, 30.0 x 100.0 mm, 110 parts (1 on the bottom side), 52 nets.

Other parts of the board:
kibuzzard-691CA83A: G***; kibuzzard-691CA83A
kibuzzard-691CA85F: G***; kibuzzard-691CA85F
kibuzzard-691CA756, kibuzzard-691CA756#2: G***; kibuzzard-691CA756
kibuzzard-691CA769, kibuzzard-691CA769#2: G***; kibuzzard-691CA769
kibuzzard-691CAAF4: G***; kibuzzard-691CAAF4
kibuzzard-692B200D: G***; kibuzzard-692B200D
kibuzzard-692B208F: G***; kibuzzard-692B208F
kibuzzard-6926CBC7: G***; kibuzzard-6926CBC7
kibuzzard-6926CC00: G***; kibuzzard-6926CC00
kibuzzard-6926CC2A: G***; kibuzzard-6926CC2A
kibuzzard-6926CC4E: G***; kibuzzard-6926CC4E
kibuzzard-6926CC47: G***; kibuzzard-6926CC47
kibuzzard-6926CCE2: G***; kibuzzard-6926CCE2
kibuzzard-6926CCF6: G***; kibuzzard-6926CCF6
kibuzzard-6926CD00: G***; kibuzzard-6926CD00
kibuzzard-6926CD0F: G***; kibuzzard-6926CD0F
kibuzzard-6926CD20: G***; kibuzzard-6926CD20

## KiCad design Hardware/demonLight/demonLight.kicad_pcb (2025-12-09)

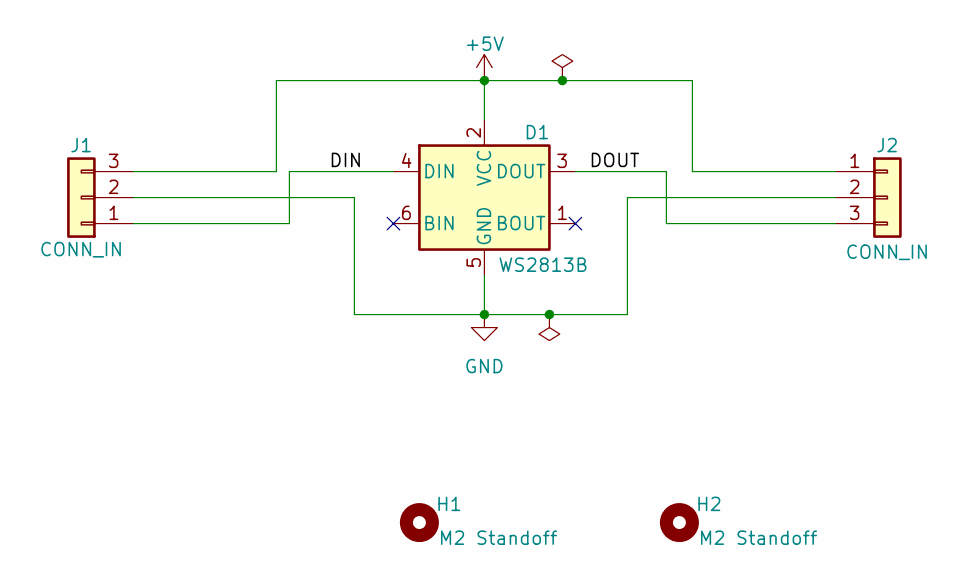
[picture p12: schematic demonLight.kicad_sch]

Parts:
D1: WS2813B; LED_WS2812_PLCC6_5.0x5.0mm_P1.6mm
H1, H2: M2 Standoff
J1, J2: CONN_IN; JST_PH_S3B-PH-K_1x03_P2.00mm_Horizontal

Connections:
+5V: D1.2 (VCC), J1.3, J2.1
/DIN: D1.4 (DIN), J1.1
/DOUT: D1.3 (DOUT), J2.3
GND: D1.5 (GND), J1.2, J2.2


Board: 2 copper layers, 65.0 x 30.0 mm, 7 parts (0 on the bottom side), 4 nets.

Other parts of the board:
kibuzzard-692CA1C6: G***; kibuzzard-692CA1C6
kibuzzard-692CA1CF: G***; kibuzzard-692CA1CF

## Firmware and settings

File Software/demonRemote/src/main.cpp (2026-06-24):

#include <Arduino.h>

#include "bat_indicator.h"
#include "charger_status.h"
#include "espnow_comm.h"
#include "pins.h"

// Send repeat interval while a button is held
static const uint32_t SEND_INTERVAL_MS = 80;

static uint32_t s_last_send_ms = 0;
static uint16_t s_last_battery_mv = 0;

void setup() {
    Serial.begin(115200);
    while (!Serial) delay(10);  // wait for USB CDC to enumerate

    pinMode(PIN_BTN_WING_UP, INPUT_PULLUP);
    pinMode(PIN_BTN_WING_DOWN, INPUT_PULLUP);
    pinMode(PIN_BTN_LED, INPUT_PULLUP);
    pinMode(PIN_BTN_SHOW_BATTERY, INPUT_PULLUP);

    bat_indicator_init();
    charger_status_init();
    espnow_init();
}

void loop() {
    bool wingUp = digitalRead(PIN_BTN_WING_UP) == LOW;
    bool wingDown = digitalRead(PIN_BTN_WING_DOWN) == LOW;
    bool led = digitalRead(PIN_BTN_LED) == LOW;
    bool showBattery = digitalRead(PIN_BTN_SHOW_BATTERY) == LOW;

    bool anyHeld = wingUp || wingDown || led || showBattery;

    if (anyHeld && (millis() - s_last_send_ms) >= SEND_INTERVAL_MS) {
        if (wingUp) {
            espnow_send(ButtonEvent::WING_UP);
        } else if (wingDown) {
            espnow_send(ButtonEvent::WING_DOWN);
        } else if (led) {
            espnow_send(ButtonEvent::LED);
        } else if (showBattery) {
            espnow_send(ButtonEvent::SHOW_BATTERY);
        }
        s_last_send_ms = millis();
    }

    if (espnow_has_battery_update()) {
        s_last_battery_mv = espnow_last_battery_mv();
        bat_indicator_set(s_last_battery_mv);
        Serial.printf("Battery: %u mV (%.2f V)\n", s_last_battery_mv, s_last_battery_mv / 1000.0f);
    }

    charger_status_update();
    ChargerState charger = charger_status_get();
    bat_indicator_show_charger(charger, s_last_battery_mv);
    if (charger == ChargerState::NO_INPUT) {
        bat_indicator_update();
    }
}

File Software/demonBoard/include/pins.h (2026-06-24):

#pragma once

// Motor driver (DRV8871DDA) pins
#define MOTOR_RIGHT_IN1  0
#define MOTOR_RIGHT_IN2  1
#define MOTOR_LEFT_IN1   4
#define MOTOR_LEFT_IN2   5

// RGB LED pins
#define LED_RIGHT        2
#define LED_LEFT         6
#define LED_AUX_RIGHT    8
#define LED_AUX_LEFT     9
#define LED_TAIL         10

// Power control
#define PIN_12V_ENABLE   7

// Battery voltage sense
#define BATTERY_SENSE    3

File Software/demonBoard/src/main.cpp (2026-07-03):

#include <Arduino.h>

#include "battery.h"
#include "ble_comm.h"
#include "espnow_comm.h"
#include "led.h"
#include "motor.h"

// Timeout: if no packet received within this many ms, stop motors
static const uint32_t HOLD_TIMEOUT_MS = 150;

// How often to push the wings battery reading to the phone app over BLE
static const uint32_t BLE_BATTERY_INTERVAL_MS = 2000;

// How often to re-send the current LED state, to self-correct if
// radio-induced noise (this board has no level shifter on the LED data
// lines) ever corrupts a frame.
static const uint32_t LED_REFRESH_INTERVAL_MS = 100;

static uint32_t s_last_packet_ms = 0;
static uint32_t s_last_ble_battery_ms = 0;
static uint32_t s_last_led_refresh_ms = 0;
static ButtonEvent s_active_event = ButtonEvent::LED;

void setup() {
    Serial.begin(115200);
    battery_init();
    motor_init();
    // LED init runs last so its "off" command is the final thing sent to the
    // strip's data line, in case radio bring-up (WiFi/BLE) induces any noise
    // on the LED GPIO during its own init.
    espnow_init();
    ble_init();
    led_init();
}

void loop() {
    if ((millis() - s_last_ble_battery_ms) >= BLE_BATTERY_INTERVAL_MS) {
        s_last_ble_battery_ms = millis();
        ble_notify_wings_battery(battery_read_mv());
    }

    if ((millis() - s_last_led_refresh_ms) >= LED_REFRESH_INTERVAL_MS) {
        s_last_led_refresh_ms = millis();
        led_refresh();
    }

    if (espnow_has_new_event()) {
        s_active_event = espnow_last_event();

        if (s_active_event == ButtonEvent::SHOW_BATTERY) {
            espnow_send_battery(battery_read_mv());
        } else {
            s_last_packet_ms = millis();
        }
    }

    bool timed_out = (millis() - s_last_packet_ms) > HOLD_TIMEOUT_MS;

    if (timed_out || s_active_event == ButtonEvent::SHOW_BATTERY) {
        motor_stop();
    } else if (s_active_event == ButtonEvent::WING_UP) {
        motor_up();
    } else if (s_active_event == ButtonEvent::WING_DOWN) {
        motor_down();
    } else {
        motor_stop();
    }
}

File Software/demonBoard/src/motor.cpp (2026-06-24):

#include "motor.h"

#include <Arduino.h>
#include "pins.h"

void motor_init() {
    pinMode(MOTOR_RIGHT_IN1, OUTPUT);
    pinMode(MOTOR_RIGHT_IN2, OUTPUT);
    pinMode(MOTOR_LEFT_IN1, OUTPUT);
    pinMode(MOTOR_LEFT_IN2, OUTPUT);
    motor_stop();
}

void motor_up() {
    digitalWrite(MOTOR_RIGHT_IN1, HIGH);
    digitalWrite(MOTOR_RIGHT_IN2, LOW);
    digitalWrite(MOTOR_LEFT_IN1, HIGH);
    digitalWrite(MOTOR_LEFT_IN2, LOW);
}

void motor_down() {
    digitalWrite(MOTOR_RIGHT_IN1, LOW);
    digitalWrite(MOTOR_RIGHT_IN2, HIGH);
    digitalWrite(MOTOR_LEFT_IN1, LOW);
    digitalWrite(MOTOR_LEFT_IN2, HIGH);
}

void motor_stop() {
    digitalWrite(MOTOR_RIGHT_IN1, LOW);
    digitalWrite(MOTOR_RIGHT_IN2, LOW);
    digitalWrite(MOTOR_LEFT_IN1, LOW);
    digitalWrite(MOTOR_LEFT_IN2, LOW);
}

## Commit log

2025-12-09 feat: Initial commit
    [Microcontroller.kicad_sch, Motor_drivers.kicad_sch, battery_charger.kicad_sch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]
2025-12-21 fix: Fix 5V connection
    [demonBoard.kicad_pcb]
2026-01-05 doc: Add schematic pdf
    [Microcontroller.kicad_sch, Motor_drivers.kicad_sch, battery_charger.kicad_sch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]
2026-01-08 feat: Add ibom.html
    [voltage_regulators_and_voltage_sense.kicad_sch]
2026-01-16 Change resistors for leds
    [Microcontroller.kicad_sch, demonBoard.kicad_pcb, voltage_regulators_and_voltage_sense.kicad_sch]
2026-01-17 Feat: Basic program
    [demonBoard.kicad_pcb]
2026-06-21 chore: Add images to Git LFS
    Track images and PDFs with LFS, move images to images/ directory, and remove old root-level jpegs.
2026-06-24 Turn off the indicator leds when charging is disconnected.
2026-06-24 cleanup: Delete old arduino files
